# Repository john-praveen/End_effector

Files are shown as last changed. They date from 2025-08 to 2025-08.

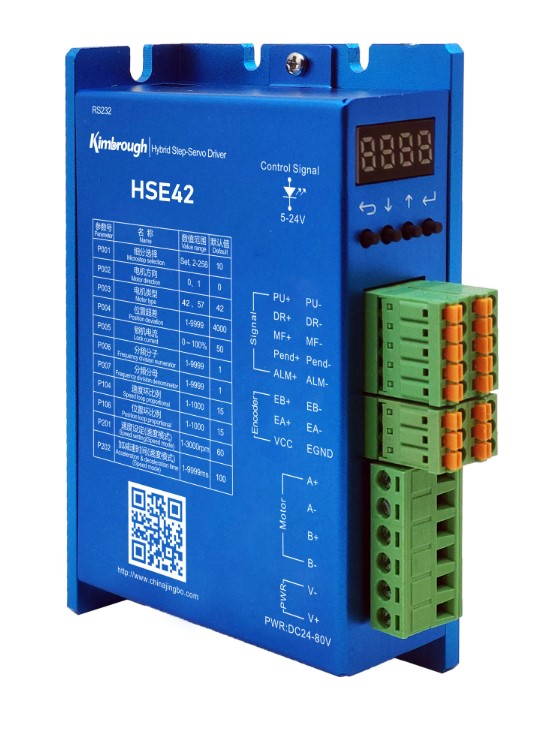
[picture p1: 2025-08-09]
Pictures/Components/Motor driver.jpg

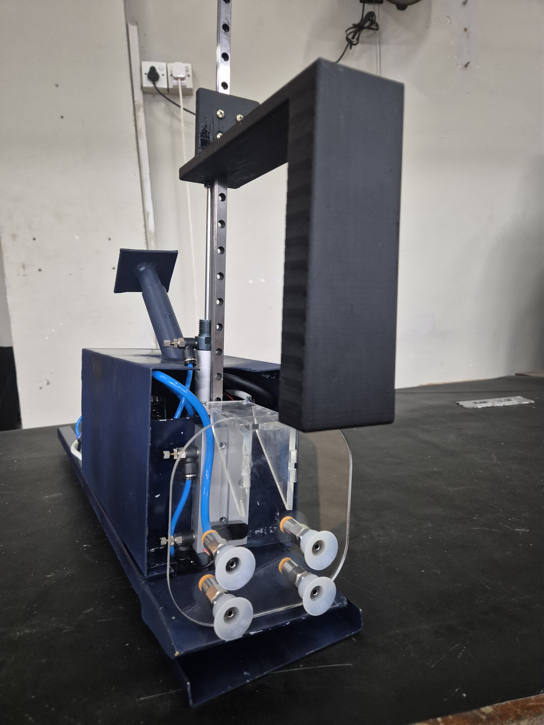
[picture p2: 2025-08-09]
Pictures/Process/3 final assembly.jpg

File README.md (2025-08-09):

# End Effector for Robotic Arm

This project is part of the **Engineering Design Realization** course at the **University of Moratuwa**. The goal is to design and implement a functional end effector that can be integrated with a robotic arm for object manipulation tasks.
The project was carried out in reference to the MCS-1-RP EOAT by WSR (https://mixedpalletizing.com/en/solutions/grippers-and-more/) and the design was a scaled down version of it.

## 🛠️ Project Overview

The end effector is designed to:
- Vaccuum grip and place boxes in warehouse/ super market settings
- Be controlled via microcontroller or external driver
- Interface with a robotic manipulator system/ Host

The project includes:
- Mechanical design (CAD)
- Electrical control (e.g., Pneumatic controls,motor drivers, communication with the host)
- Firmware (AVR - ATMEGA 2560)
- Prototyping and testing

## 📁 Repository Structure

```
End_Effector/
├── CAD/              # 3D models and design files
├── Firmware/         # Microcontroller code (AVR)
├── Schematics_PCB/   # Circuit diagrams
├── Images/           # Build photos or diagrams
└── README.md         # Project documentation
```

## 🔧 Tools & Technologies

- CAD Software:SolidWorks
- Microcontroller: ATMEGA 2560
- Actuators: Stepper motor with encoder feedback/ Single and double rod pneumatic pistons/ Vaccuum suction cups
- Programming Language: C/C++

##This project is a joint effort of
- Muftee Mysaan
- Kavishka Jayakody
- Pravindu Gunathilaka
- Rajinthan Rajeshkumar
- John Praveen
- Nilakna Warusavithana
- Venumi Gunasekara

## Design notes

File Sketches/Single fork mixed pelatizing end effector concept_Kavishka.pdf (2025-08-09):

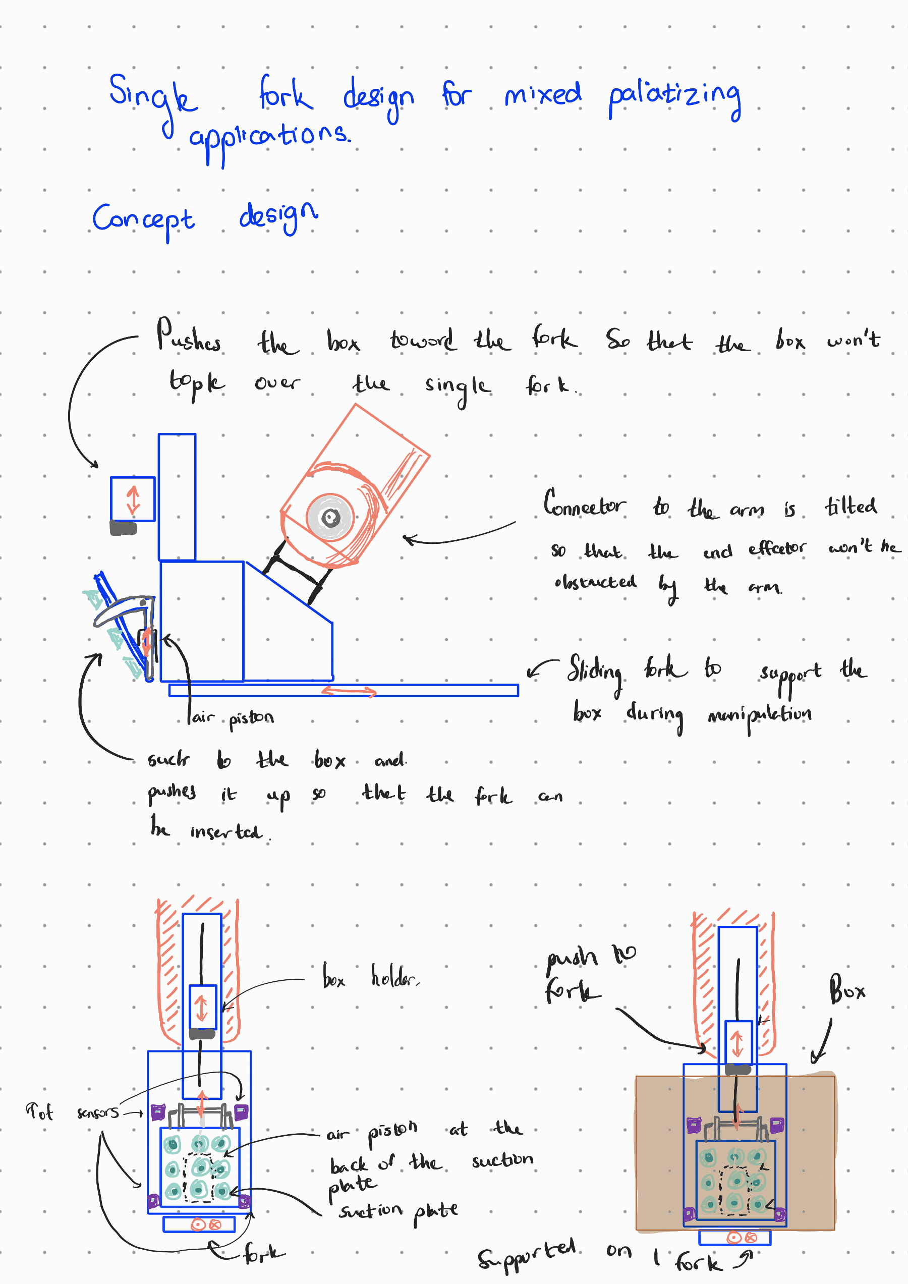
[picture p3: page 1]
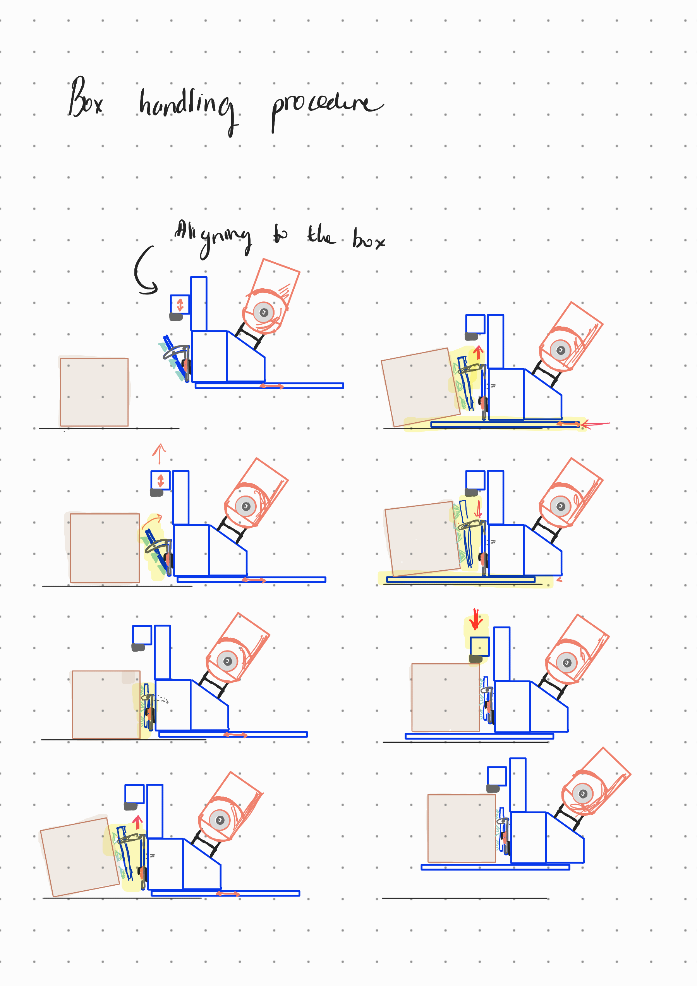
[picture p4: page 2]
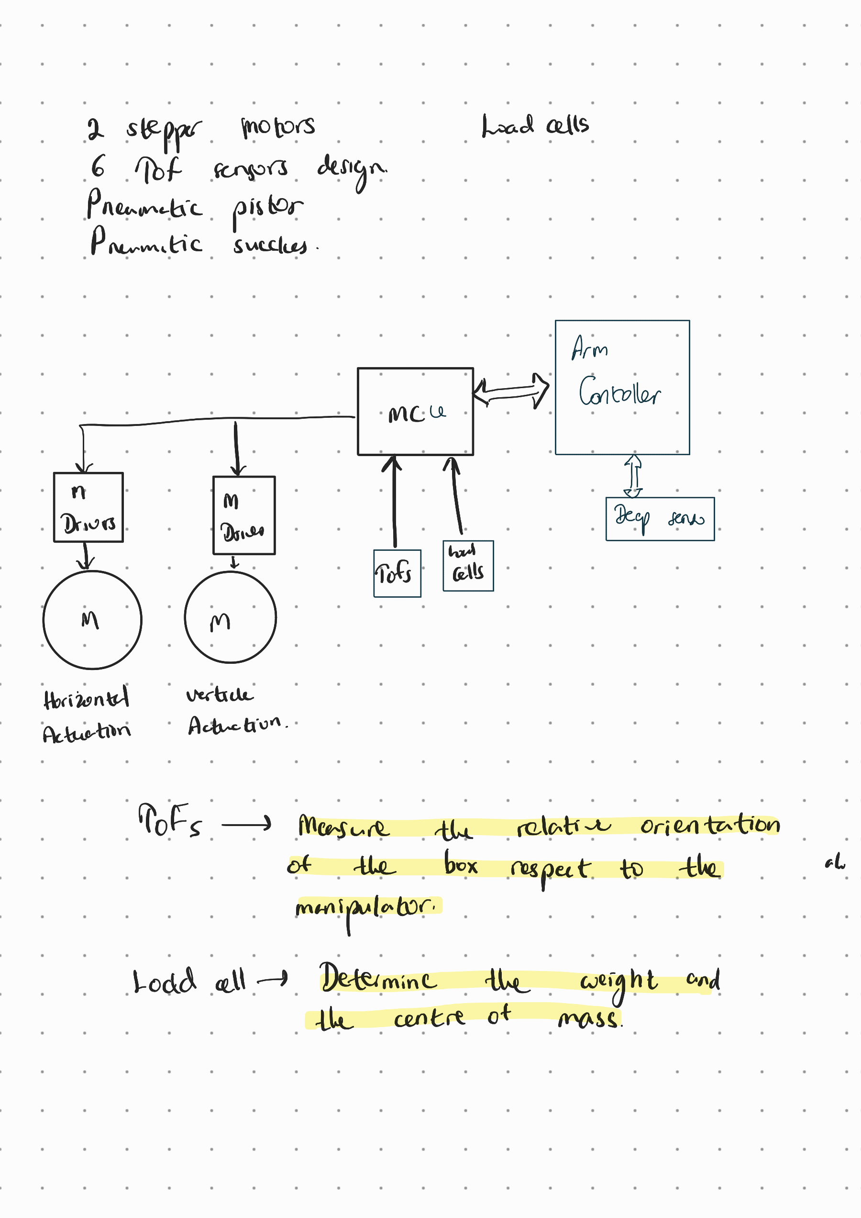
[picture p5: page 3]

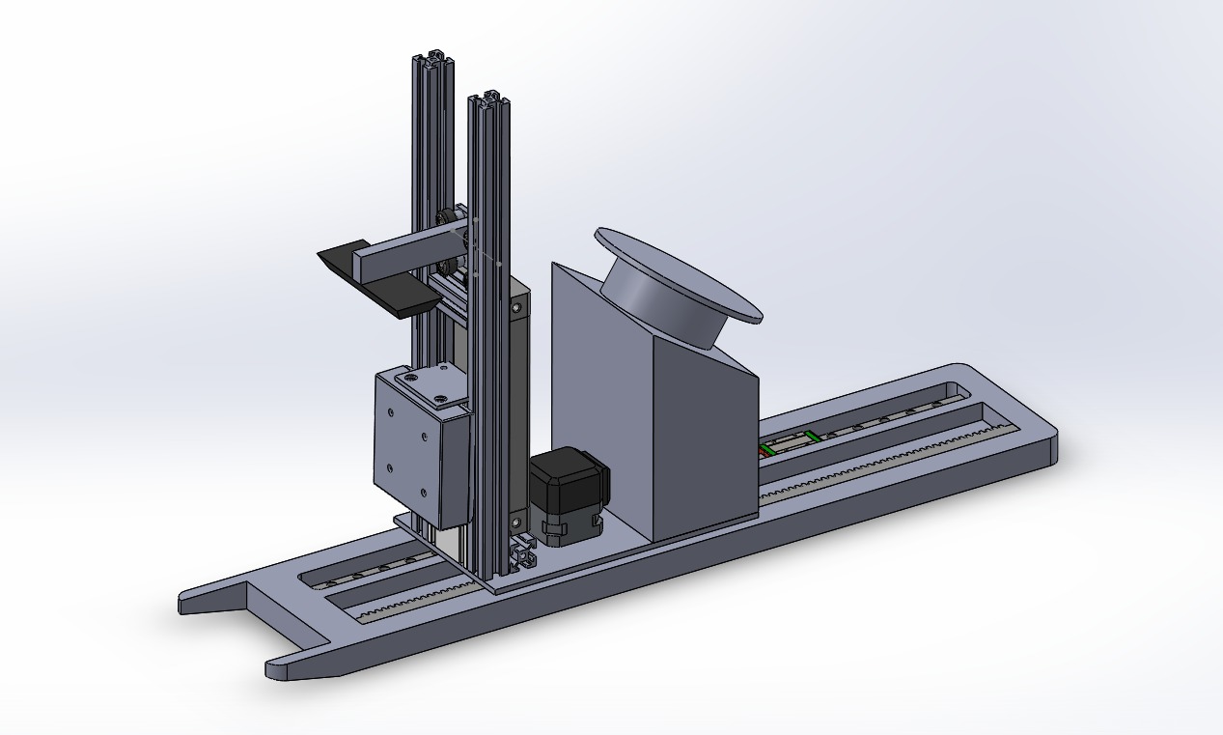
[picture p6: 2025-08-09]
Pictures/Concepts/3D Concept 1.jpg

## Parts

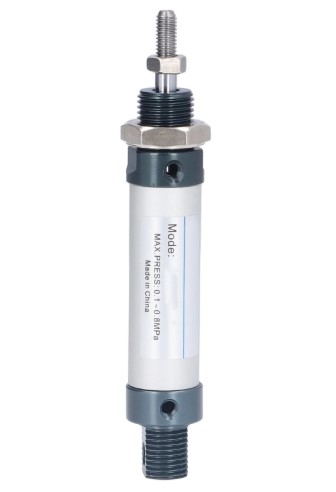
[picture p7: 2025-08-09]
Pictures/Components/single rod cylinder.jpg

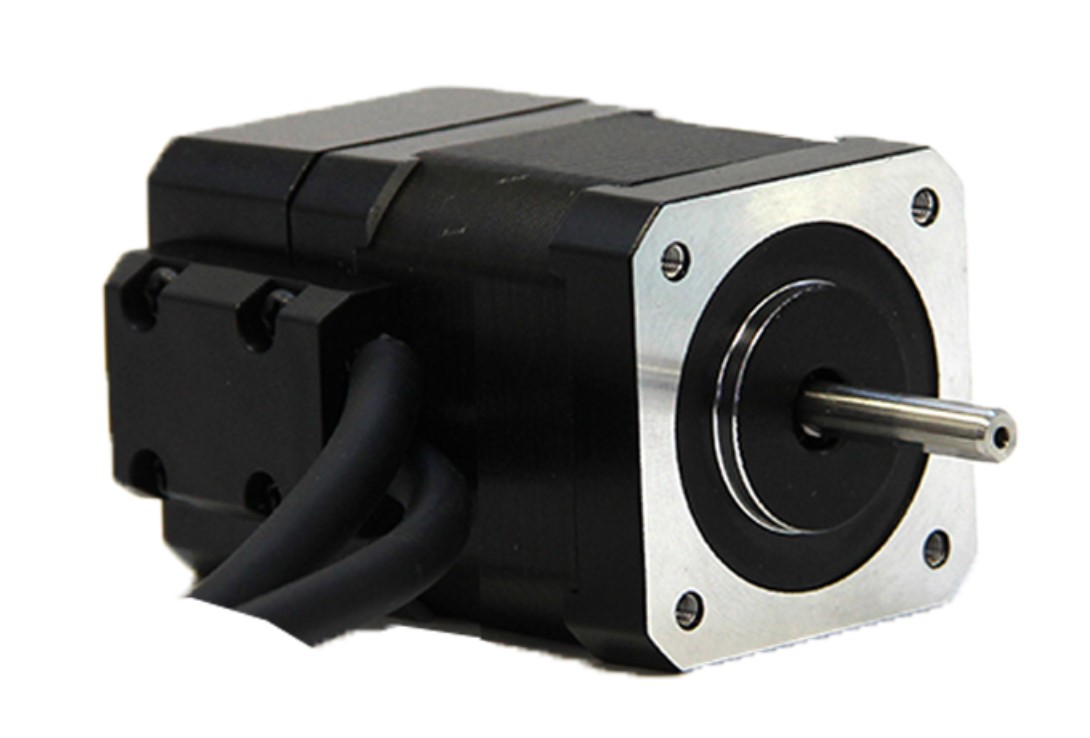
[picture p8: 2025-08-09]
Pictures/Components/Stepper motor.jpg

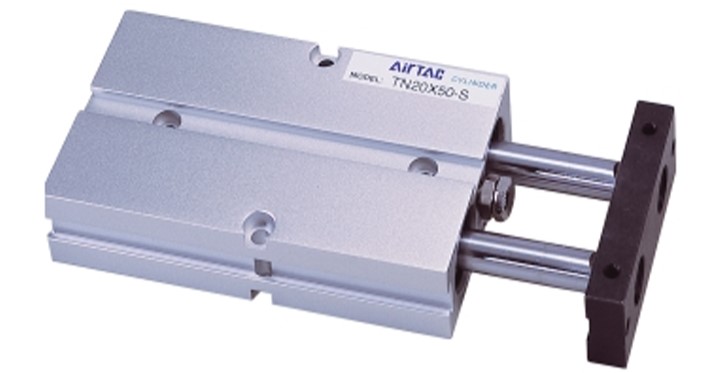
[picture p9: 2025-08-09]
Pictures/Components/double rod cylinder.jpg

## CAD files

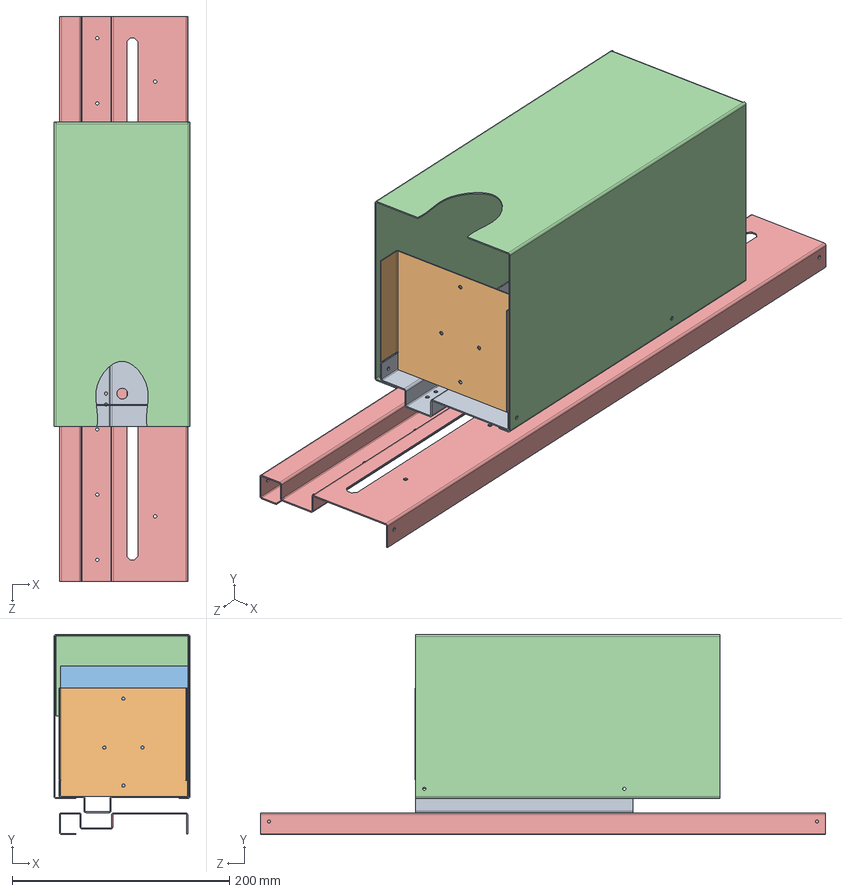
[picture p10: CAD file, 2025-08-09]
3D Models/Sheet metal/Assembly.SLDASM
125.0 x 184.0 x 520.0 mm
base_flange
front_plate
Backplate
Outer Cover
fork

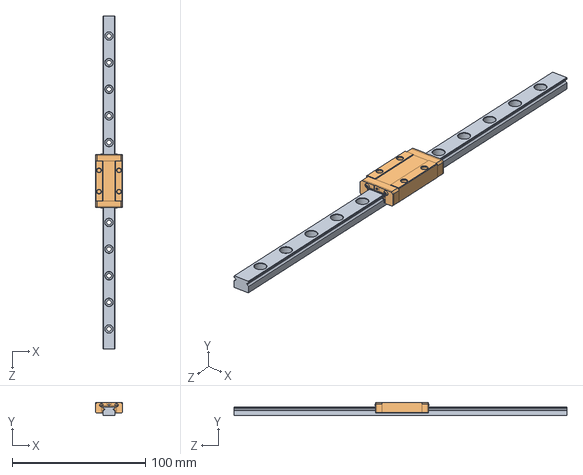
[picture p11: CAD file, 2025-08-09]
3D Models/guide rails/ver.2/MGN9-250.SLDASM
20.0 x 10.0 x 250.0 mm
MGN9
MGN9-H

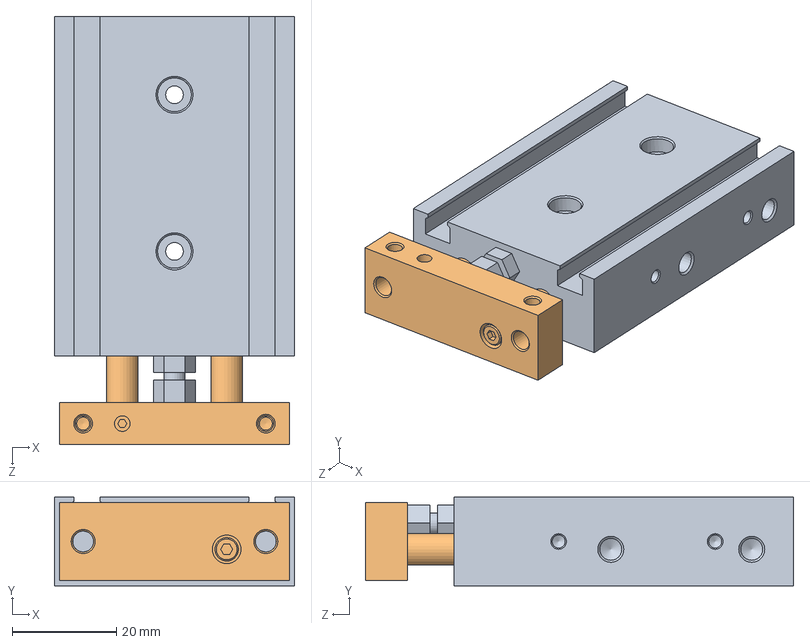
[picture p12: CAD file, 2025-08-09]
3D Models/Pneumatics/CXSM10-10/CXSM10-10.SLDASM
46.0 x 17.0 x 82.0 mm
CXSM10-10_cyl_cxs
CXSM10-10_pr_cxs

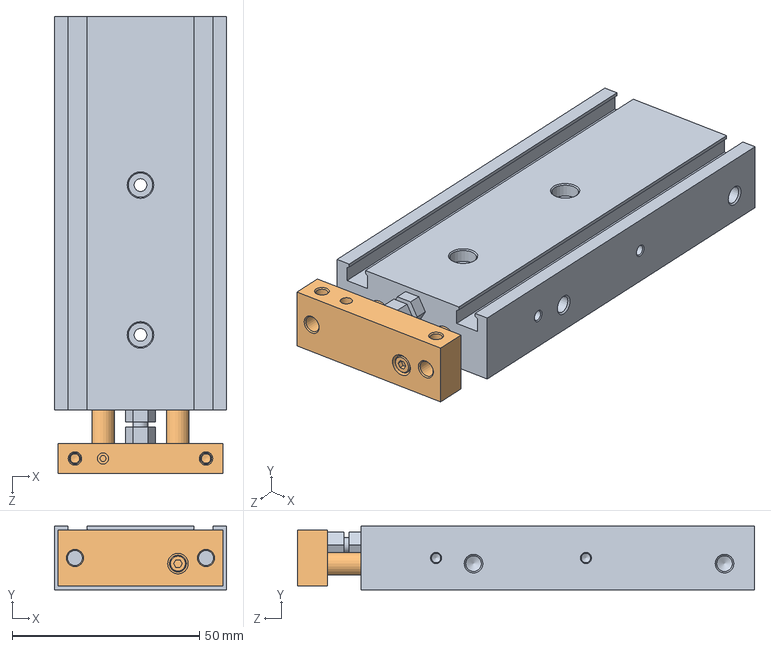
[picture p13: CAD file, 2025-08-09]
3D Models/Pneumatics/CXSM10-50/CXSM10-50.SLDASM
46.0 x 17.0 x 122.0 mm
CXSM10-50_cyl_cxs
CXSM10-50_pr_cxs

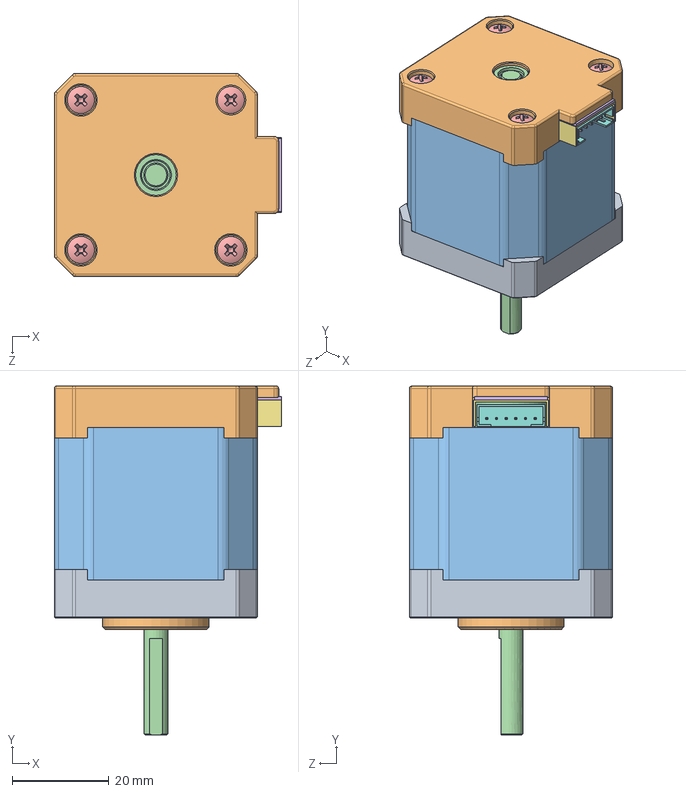
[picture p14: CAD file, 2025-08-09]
3D Models/Stepper motor/NEMA 17 Stepper Motor 48mm/NEMA 17 Stepper Motor 48mm.SLDASM
47.0 x 72.2 x 42.0 mm
Cuerpo007 x 6
Cuerpo
Cuerpo002
Cuerpo003
M3x37-Tornillo x 4
Cuerpo004
Cuerpo005
Cuerpo006
Cuerpo008
Cuerpo001

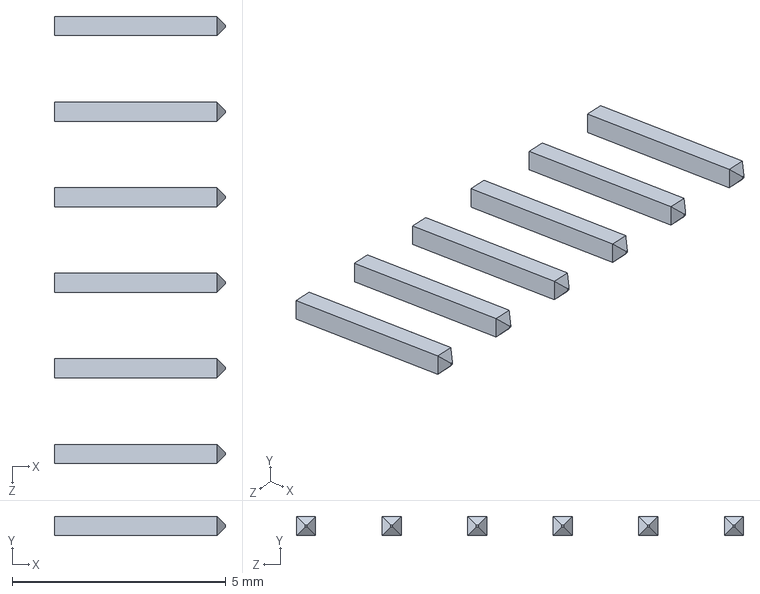
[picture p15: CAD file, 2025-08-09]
3D Models/Stepper motor/NEMA 17 Stepper Motor 48mm/Pines.SLDASM
4.00 x 0.45 x 10.4 mm
Cuerpo007 x 6

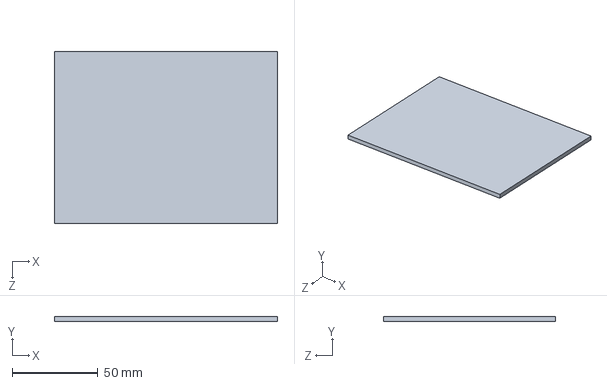
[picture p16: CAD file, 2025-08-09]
3D Models/base/Base.SLDPRT
130.0 x 3.00 x 100.0 mm

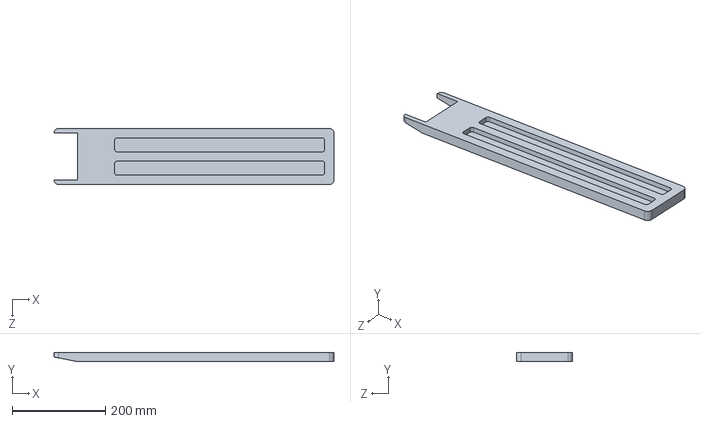
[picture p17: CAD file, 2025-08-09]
3D Models/fork/fork.SLDPRT
600.0 x 20.0 x 120.0 mm

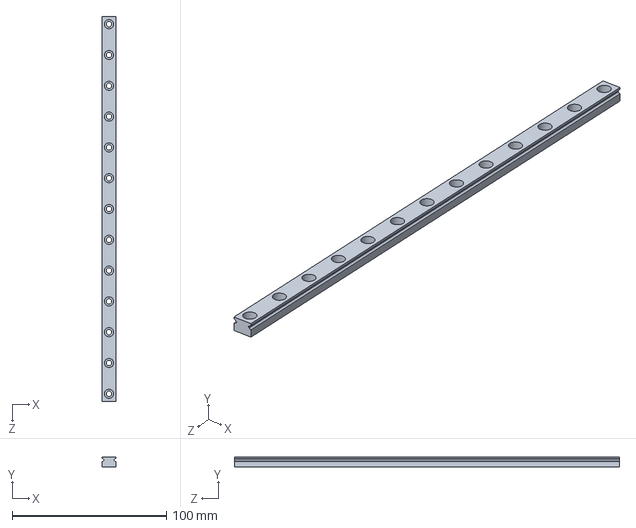
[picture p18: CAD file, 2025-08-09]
3D Models/guide rails/v1_MGN9_250.SLDPRT
9.00 x 6.50 x 250.0 mm

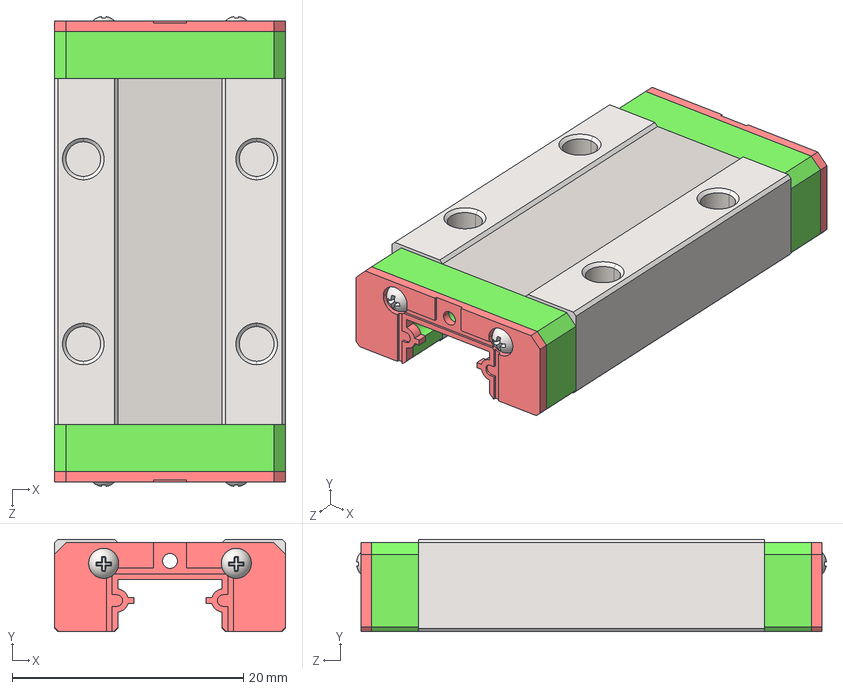
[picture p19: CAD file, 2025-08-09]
3D Models/guide rails/ver.2/MGN9-H.STEP
20.0 x 8.00 x 40.7 mm

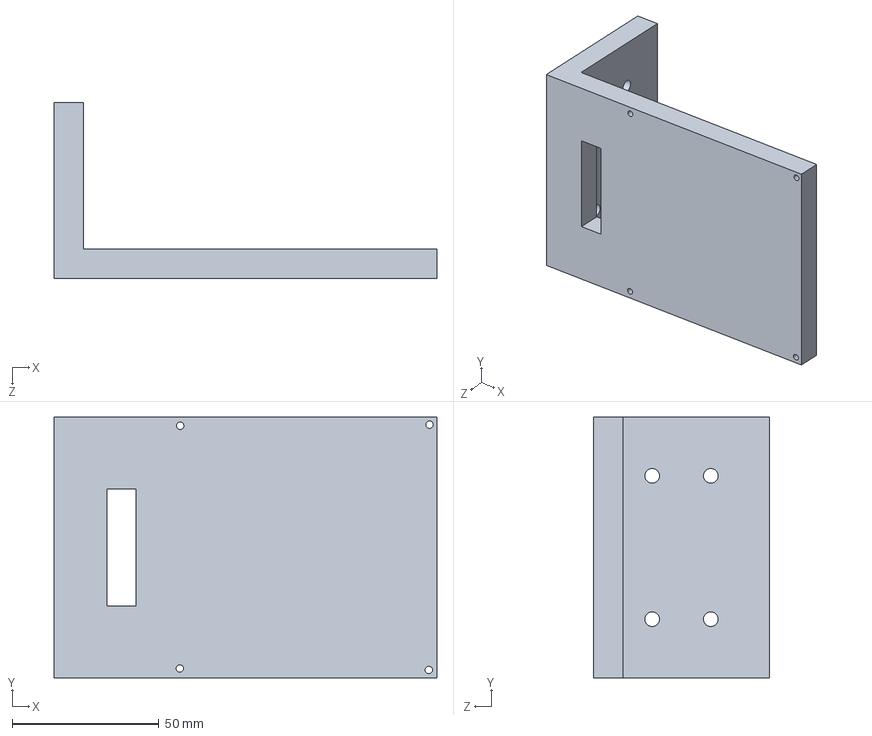
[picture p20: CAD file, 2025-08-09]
3D Models/John/end_effector_solidworks/parts/pcb_mount_F.SLDPRT
130.7 x 88.9 x 60.0 mm

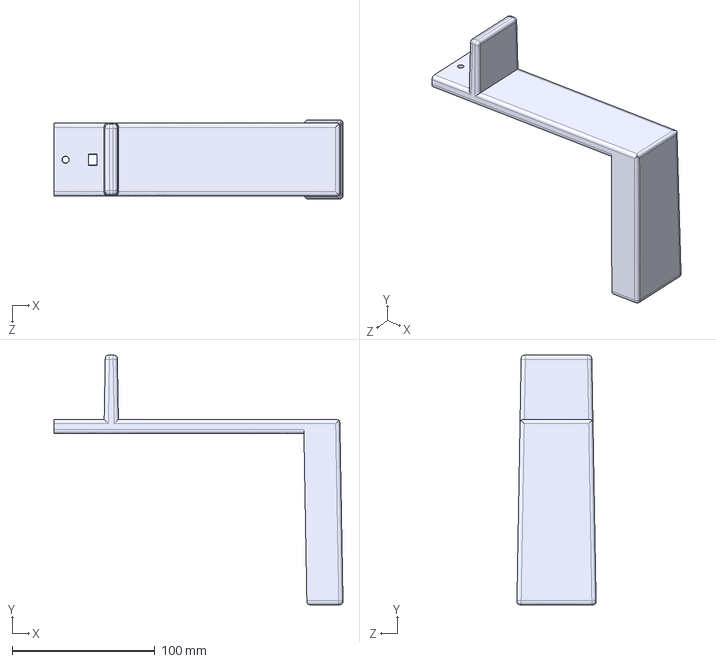
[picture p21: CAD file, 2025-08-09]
3D Models/John/end_effector_solidworks/stp/top support.STEP
202.6 x 175.0 x 55.5 mm

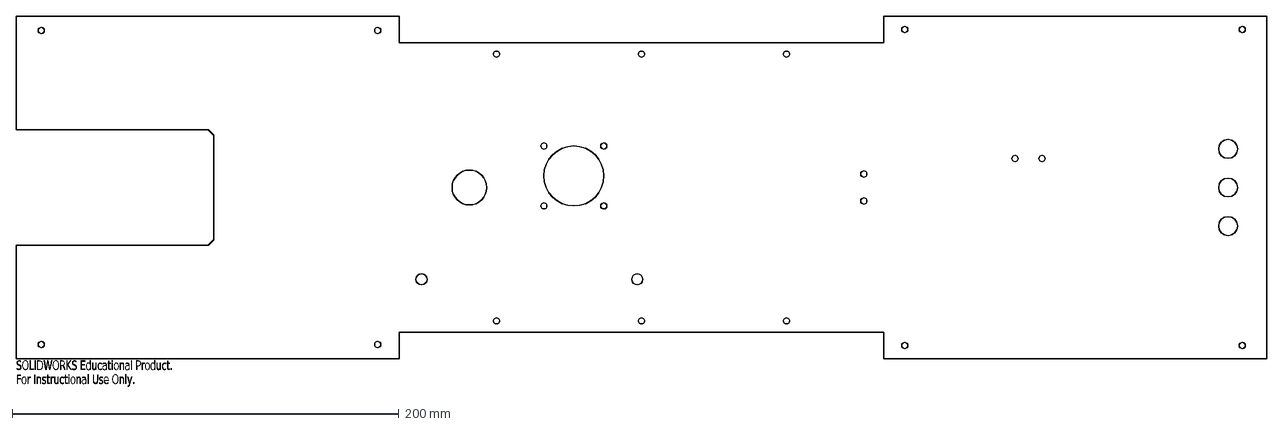
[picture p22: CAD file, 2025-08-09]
3D Models/Sheet metal/Fabrication Outputs/Flat pattern - body_flat.DXF
SOLIDWORKS Educational Product.
For Instructional Use Only.

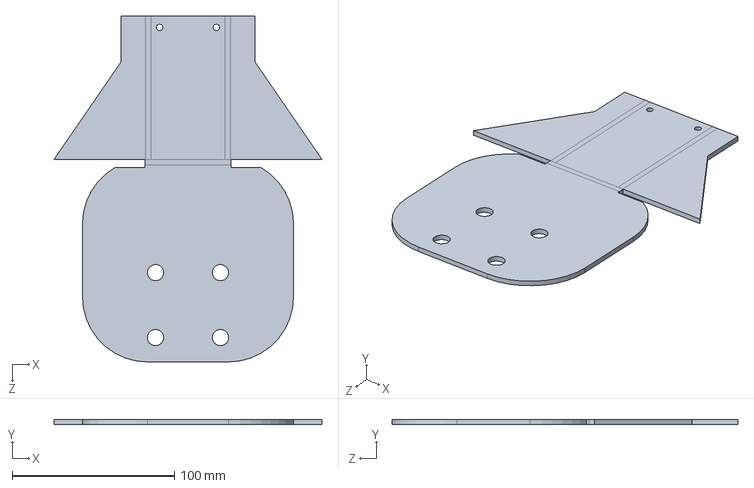
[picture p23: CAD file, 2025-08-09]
3D Models/Sheet metal/Suction Pad/sheet metal suction pad.SLDPRT
165.1 x 3.00 x 213.0 mm

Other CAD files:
3D Models/guide rails/MGN9.SLDASM
3D Models/Pneumatics/CXSM10-10/CXSM10-10_pr_cxs.sldprt
3D Models/Pneumatics/CXSM10-50/CXSM10-50_pr_cxs.sldprt
3D Models/Sheet metal/Top Support/sheet metal top support venumi.SLDPRT
3D Models/John/end_effector_solidworks/parts/top support.SLDPRT
3D Models/John/end_effector_solidworks/parts/vaccum_plate.SLDPRT
3D Models/John/end_effector_solidworks/stp/pcb_mount.STEP
3D Models/John/end_effector_solidworks/stp/vaccum_plate.STEP
3D Models/Pneumatics/CXSM10-10/CXSM10-10_cyl_cxs.sldprt
3D Models/Pneumatics/CXSM10-50/CXSM10-50_cyl_cxs.sldprt
3D Models/Sheet metal/Backplate.SLDPRT
3D Models/Sheet metal/Fabrication Outputs/Flat pattern - cover_flat.DXF
3D Models/Sheet metal/Fabrication Outputs/Flat pattern - fork_flat.DXF
3D Models/Sheet metal/Fabrication Outputs/Flat pattern - metal_back.DXF
3D Models/Sheet metal/Outer Cover.SLDPRT
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

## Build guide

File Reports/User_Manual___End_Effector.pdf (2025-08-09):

# User Manual

# End Effector

Group 07
Document Version 1.0

May 2025

## Contents

1 Preface | 3
2 Getting Started | 3
3 Control Commands | 7
4 Assembly Instructions | 8
5 Maintenance Guidelines | 12
6 Technical Specifications | 13

## 1 Preface

### 1.1 Target Audience

This document is intended for integrators who design and install complete robot applications. Personnel working with the end-effector are expected to have the following expertise:

- Basic knowledge of mechanical systems
- Basic knowledge of electronic and electrical systems
- Basic knowledge of the robot system

### 1.2 Intended Use

The end-effector is designed for grabbing objects, installed on the end effector of a robot, typically used in pick and place applications.

### 1.3 Safety Notice

A risk assessment is required for each application the end-effector is a part of. It is important that all safety instructions are followed. The safety instructions are limited to the end-effector only, and do not cover the safety precautions of a complete application.

Below are some (but not all) potentially dangerous situations.

- Entrapment of fingers between the sliding rail and the body.
- Entrapment of fingers between the rail and/or vertical stabilizer and the body.
- Objects falling out of the end-effector e.g. due to misalignment of robot arm or high acceleration from robot arm.

## 2 Getting Started

### 2.1 Mounting

The end-effector is attached to the robot arm using a welding neck flange, following the ISO 9409-1 standardized mounting interface. Proper alignment is ensured through the use of suitable screws positioned on a pitch circle diameter.

Mounting Parameters (ISO 9409-1)

- d1 : 37.5 | (Pitch Circle Diameter)
- N : 4 | (Number of threaded holes)
- d4 : M6 | (Thread size of holes)

### 2.2 Operation

### 2.2.1 Communication with PC

The end-effector communicates the following information with the robot controller PC:

- Angle: Angle between the end-effector and the object to be picked.
- Distance: Distance between the end-effector and the object to be picked.

The robot controller is expected to ensure proper alignment and positioning of the end-effector for successful gripping operation.

### 2.2.2 Picking the Object

Once proper alignment and positioning is ensured, the pick command must be issued to the end-effector by the robot controller PC.

Once the command is given, the following steps will take place:

- Suction: The vacuums will activate and suction will hold the object against the suction pad.
- Raising: The suction pad will rise up, lifting the side of the object.
- Rail: The rail will slide under the object.
- Top Support: The vertical stabilizer will move down onto the object, providing further stabilization.
- Remove Suction: Suction will be removed once the object is stable.

### 2.2.3 Transporting the Object

The robot arm is responsible for transporting the object to the correct destination and ensuring correct alignment.

### 2.2.4 Placing the Object

Once proper alignment and positioning is ensured, the place command must be issued to the end-effector by the robot controller PC.

Once the command is given, the following steps will take place:

- Rail: The sliding rail will move out from under the object, resting the object at the target location.
- Top Support: The top support will raise and the object will be completely released by the end-effector.

### 2.3 Mechanical Dimensions

### 2.3.1 Fork

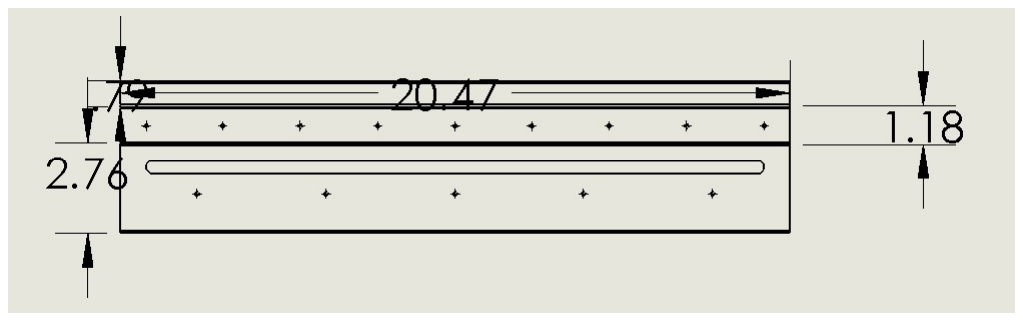
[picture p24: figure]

Figure 1: Fork Dimensions

### 2.3.2 Base Flange

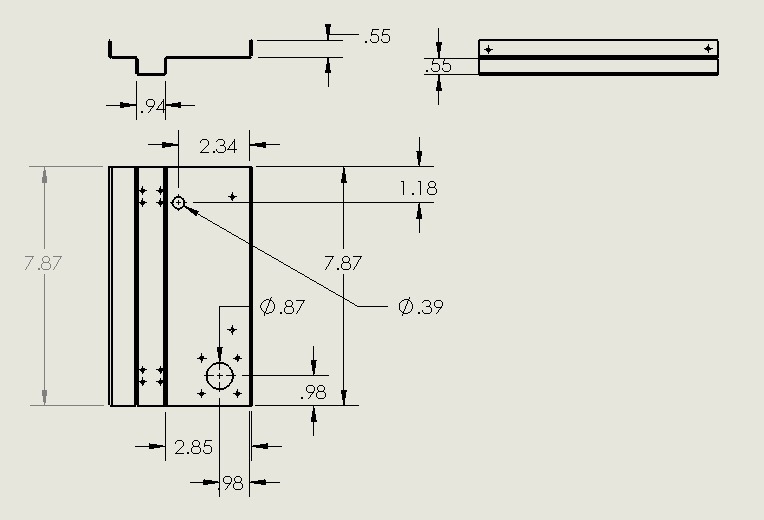
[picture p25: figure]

Figure 2: Base Flange Dimensions

### 2.3.3 Outer Cover

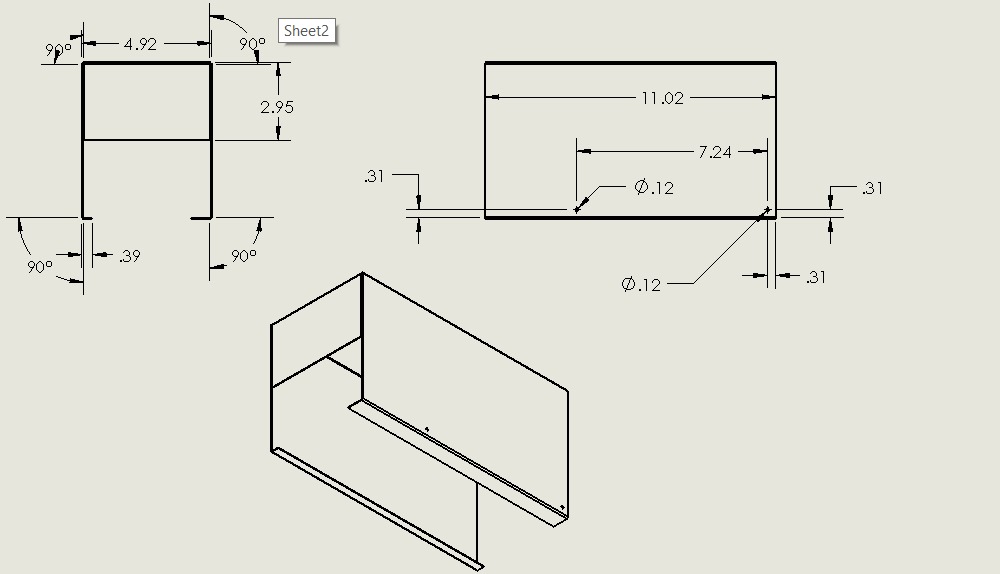
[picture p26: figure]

Figure 3: Outer Cover Dimensions

### 2.3.4 Back Plate

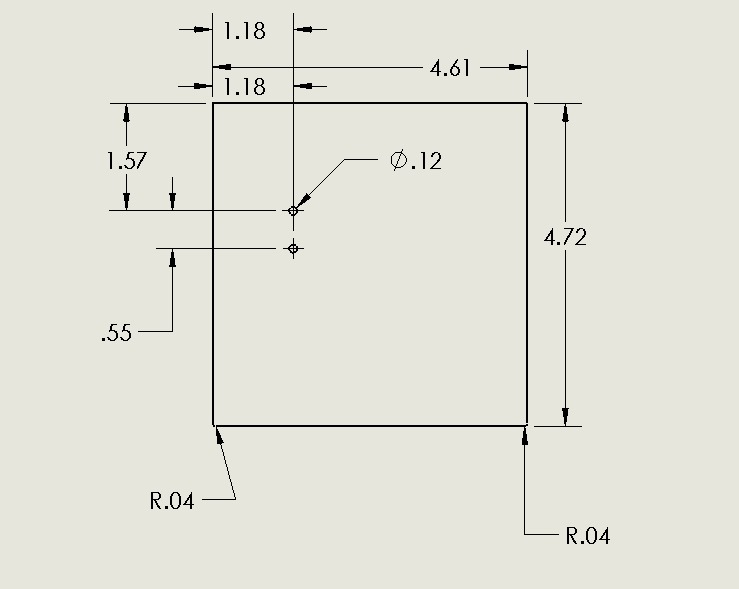
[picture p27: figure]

Figure 4: Back Plate Dimensions

### 2.3.5 Front Plate

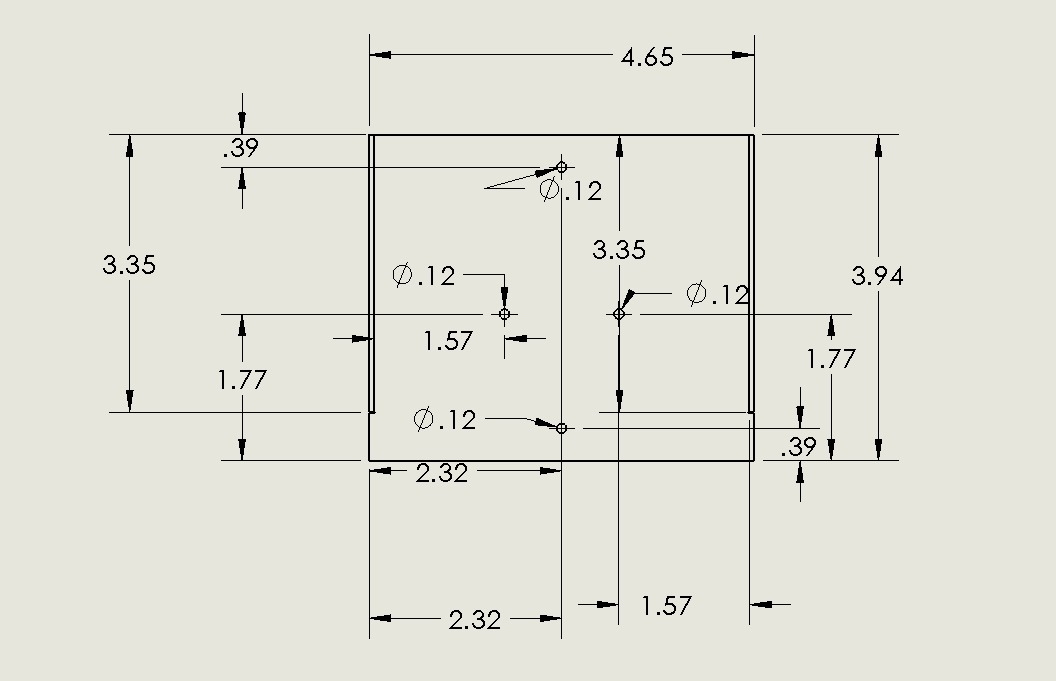
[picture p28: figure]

Figure 5: Front Plate Dimensions

### 2.3.6 Gear wheel and Rack

- Pinion Gear:

– Module: 1 mm

– Teeth: 20

– Pitch Diameter: 20 mm

– Bore: 5mm (D-type with cut at 4.5mm)

- Rack:

– Module: 1 mm

– Face width: ≥ 10 mm

– Length: 500 mm

### 2.4 Load Capacity

The end-effector has an operational capacity of 1kg uniformly weighted boxes. Exceeding the weight limit may result in structural failure and/or injury.

### 2.5 Connections

### 2.5.1 Pneumatic Connections

Guide the connections for the solenoids and the vacuum suction pads through the groove cut into the base.

Connect 4mm PU tubes from the two double solenoids to the single rod and double rod pistons (each piston must have two tubes.) Connect 4mm tubes from the single solenoid to the suction cups.

Connect the vacuum to the single solenoid and compressor the the two double solenoids using 6mm PU tubes. The solenoid tubes and vacuum tubes must be connected to a compressor with the following specifications.

### 2.5.2 Power Supply

The gripper is designed to operate with a 24V DC power supply. Ensure the power source is regulated and within the specified voltage range for safe and reliable operation. Guide the power supply through the same groove in the base.

Table 1: Pneumatic Specifications

Parameter | Value
Pressure | 6 bar
Air Supply Tube Diameter | Ø12 mm
Airflow (including vacuum) | 40 l/min
Minimum Air Quality | ISO 8573-1:2010 7 : 4 : 4

## 3 Control Commands

The end-effector is controlled via UART communication with the host system (typically a PC or microcontroller). The following commands must be transmitted over UART to initiate the respective operational sequences. The communication protocol uses 8 data bits, no parity, and 1 stop bit (8N1), as shown in Figure 6.

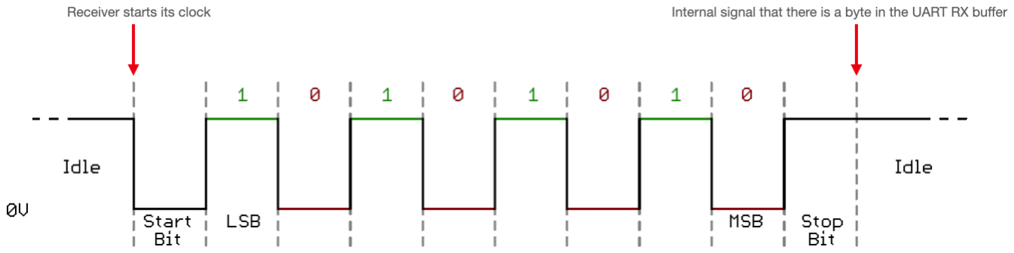
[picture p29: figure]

Figure 6: UART Protocol: 8 data bits, 1 stop bit

### 3.1 Pick Command

To initiate the picking sequence, transmit the command CMD GRIPPER PICK. This command autonomously executes the full gripping and lifting process. No further step-by-step commands are required.

### 3.2 Place Command

To initiate the release sequence, transmit the command CMD GRIPPER RELEASE. This will fully execute the object release process, including the lowering and unclamping actions.

### 3.3 Debug Commands

For system-level debugging and verification, the following individual control commands can be used. These allow manual actuation of subsystems for testing. Warning: Ensure the workspace around the end-effector is clear before issuing debug commands to avoid damage or injury.

- CMD TOP GRIPPER
- CMD FORK
- CMD VACUUM GRIPPER
- CMD VACUUM UP

## 4 Assembly Instructions

Follow the steps outlined below to correctly assemble the end-effector. All fasteners specified are M3 unless otherwise stated.

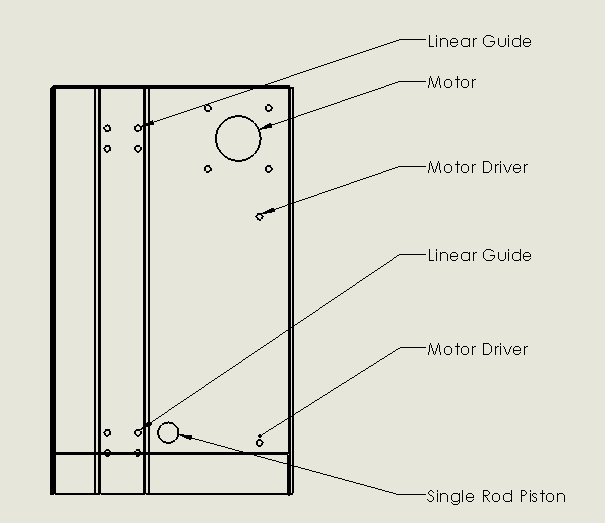
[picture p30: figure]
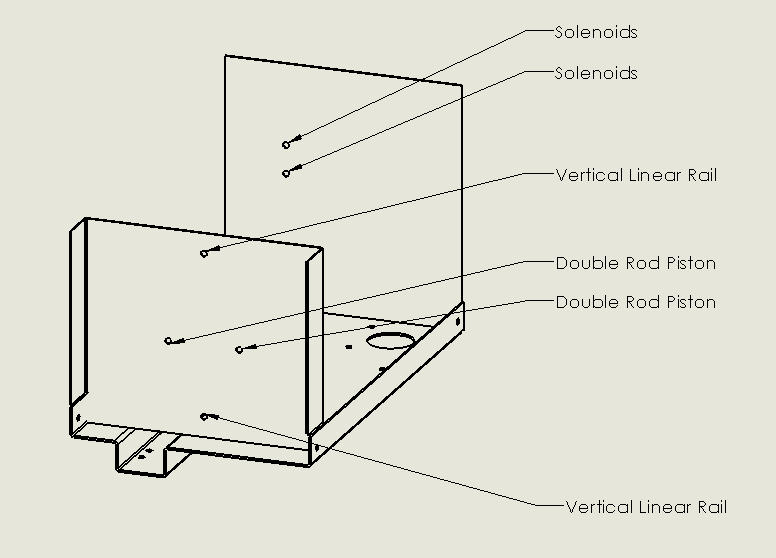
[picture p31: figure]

Figure 7: Top View - Base | Figure 8: Dimetric View - Base

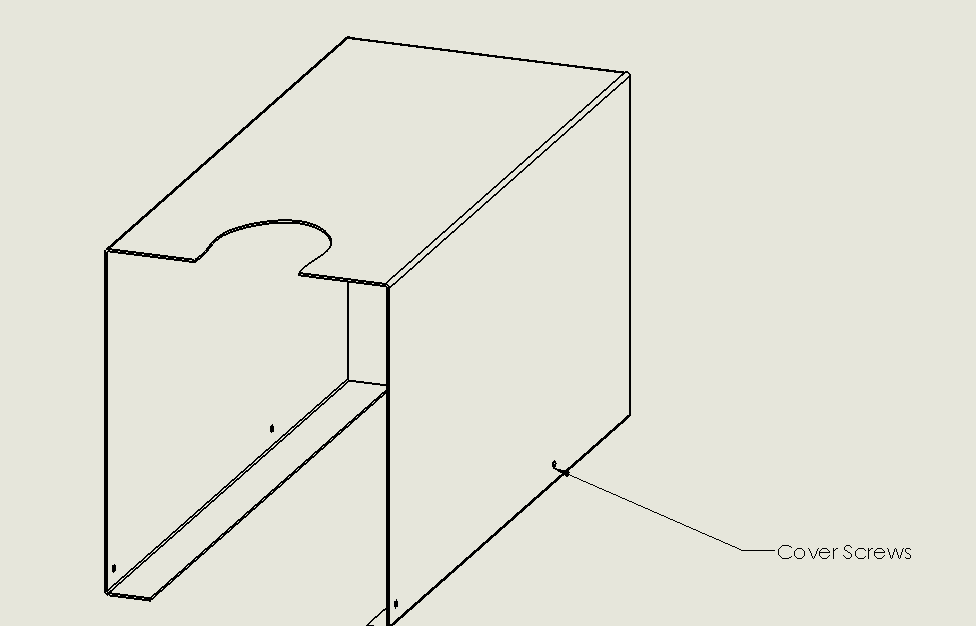
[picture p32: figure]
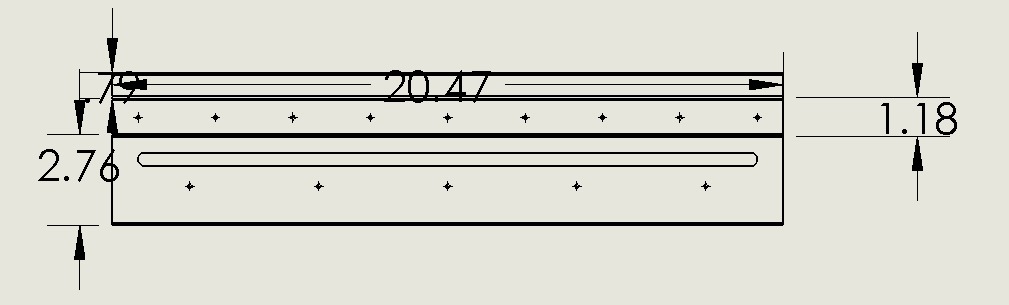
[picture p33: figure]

Figure 9: Cover | Figure 10: Fork

### 4.1 Motor Mounting

Secure the motor to the base using four 1/4-inch M3 screws and M3 nuts. Ensure that the motor shaft extends downward through the designated central opening in the base.

### 4.2 Installation of Linear Guides and Rail

Attach the linear guides to the underside of the base using four 1/4-inch M3 screws inserted from the top side. The alignment slot of the linear guide must correspond precisely with the groove on the base. After installation, insert the linear rail into the linear guide track.

### 4.3 Fork Assembly

Position the assembled base and linear rail onto the fork component, aligning the end holes of the rail with the predrilled mounting holes on the fork groove. Secure the linear rail to the fork using three 1/4-inch M3 screws and M3 nuts. Mount the rack to the underside of the fork using three M3 screws and nuts, inserted from the top side. Install the gear wheel onto the motor shaft, ensuring proper engagement with the rack teeth to allow smooth linear motion. Once complete, insert the lower fork section into the upper fork structure. Align the screw holes and fasten them using four 1/4-inch M3 screws.

### 4.4 Vertical Rail and Top Support

Fix the vertical linear rail to the base using two M3 screws and nuts, fastened from the inside. Couple the linear guide to the top support bracket, and slide the vertical rail into the guide channel to complete the vertical axis assembly.

### 4.5 Solenoids and Piston Installation

Mount the double and single solenoids to the rear panel of the base using two 4-inch M3 screws and M3 nuts. Secure the double-rod pneumatic cylinder to the front of the base using two 1/2-inch M3 screws and nuts. Attach the single-rod pneumatic piston to the base using a 12 mm bolt from underneath. Fix the top support to the piston shaft to complete the actuator assembly.

### 4.6 Motor Driver

Fasten the motor driver horizontally to the base using two 1/4-inch M3 screws and M3 nuts. Ensure that the back plate faces outward and the terminal connectors face upward.

### 4.7 PCB Integration

Install the PCB standoffs to the base and mount the PCB using eight 1/4-inch M3 screws and M3 nuts.

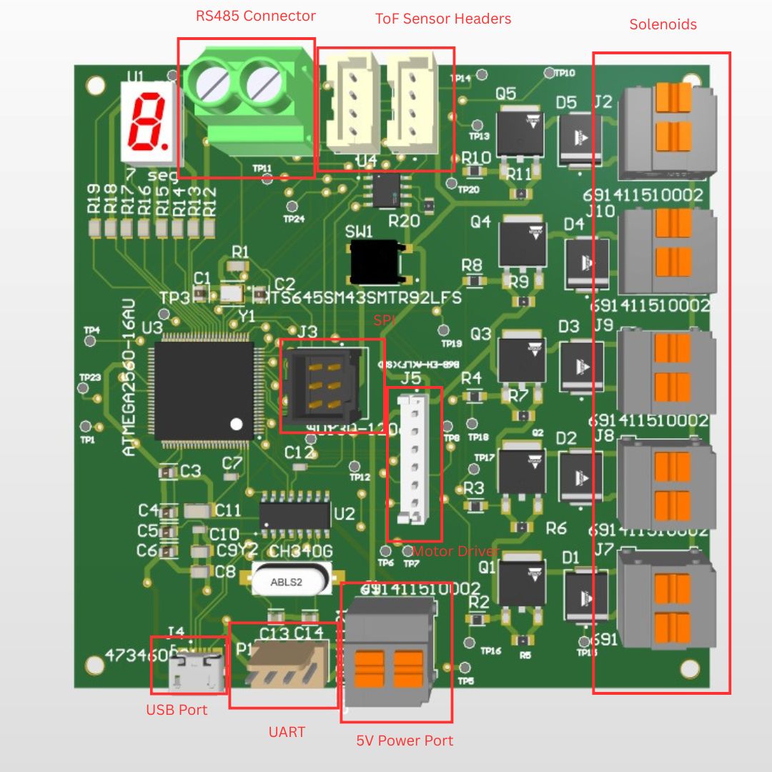
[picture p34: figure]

Figure 11: Main Connectors Annotation

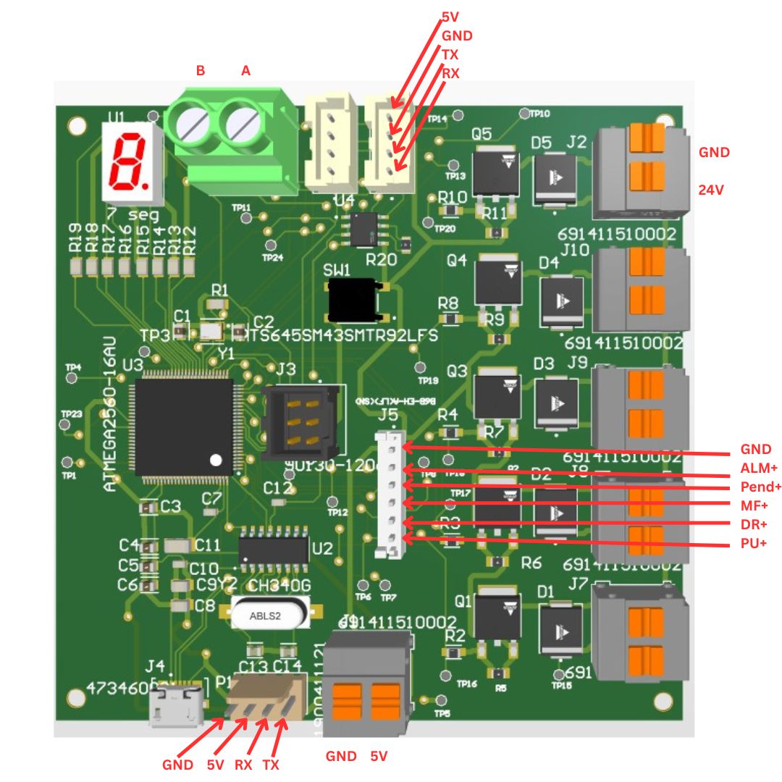
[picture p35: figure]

Figure 12: Pin Mapping

Refer to the annotated 3D PCB view for identifying the correct headers. Carefully install the ToF sensor and motor driver module onto the designated connectors as labeled. Ensure that each module is connected to its respective header—UART, SPI, solenoid, ToF, and motor driver—as shown in the pin mapping. Double-check the orientation and pin alignment to match the annotated pin assignments. Incorrect connections may result in malfunction or hardware damage.

### 4.8 Suction Plate Installation

Secure the suction plate to the top of the double-rod piston using two 1/4-inch M3 screws and M3 nuts. Connect the 4mm tubes to the suction cups and route them over the top and through the groove in the base.

### 4.9 Electrical and Pneumatic Routing

Neatly route all electrical wires and pneumatic tubing through the designated groove channel in the base.

### 4.10 Final Assembly and Mounting

Place the top enclosure over the base and secure it using four M3 screws and nuts. Finally, attach the fully assembled end-effector to the robot arm flange using a 6 mm screw and nut.

Once completed, the end effector should look similar to the following images:

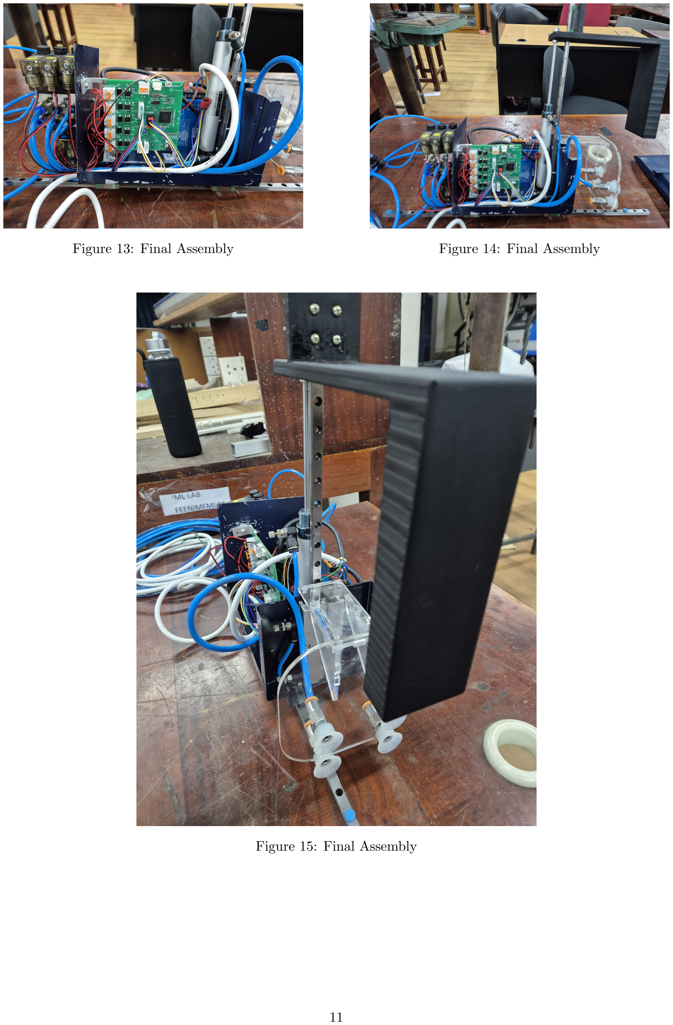
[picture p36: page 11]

Figure 13: Final Assembly | Figure 14: Final Assembly

Figure 15: Final Assembly

## 5 Maintenance Guidelines

This section outlines the preventive maintenance procedures required to ensure the long-term reliability and performance of the end-effector. All maintenance activities should be logged with date, technician name, and observations.

### 5.1 Closed-Loop Stepper Motor and Gear Mechanism

Interval: Every 250 operating hours or monthly (whichever comes first)

- Perform visual inspection for dust, debris, and oil contamination.
- Check axial and radial play in the motor shaft. Replace bearings if excessive movement is detected.
- Inspect gear teeth and rack for signs of wear, backlash, or misalignment.
- Apply high-performance synthetic gear lubricant to the gear teeth and rack.
- Conduct encoder feedback diagnostics to verify closed-loop accuracy.

### 5.2 Linear Guides and Rail

Interval: Every 100 operating hours

- Clean linear guideways with lint-free cloth and reapply lithium-based grease.
- Inspect for abnormal noise or resistance during linear motion; verify alignment and smoothness.
- Use dial indicator or laser alignment tools to detect rail deflection or misalignment.

### 5.3 Pneumatic Solenoids and Cylinders

Interval: Weekly visual inspection, full functional test every 200 cycles

- Inspect PU tubing for cracks, brittleness, or leaks.
- Verify actuation of all three double solenoids and both pistons (single and double rod) via manual override.
- Conduct air leak test using soap solution or ultrasonic leak detector.
- Check piston rods for surface pitting or sticking; re-lubricate or replace seals as necessary.
- Validate response time and holding pressure using a calibrated pneumatic test bench.

### 5.4 Vacuum Plate Assembly

Interval: Biweekly

- Check for airtight seals and vacuum pressure drop using a digital vacuum gauge.
- Inspect suction cups for deformation or wear; replace if rigidity is compromised.
- Clean contact surfaces to maintain optimal grip efficiency.

### 5.5 PCB and Electrical Components

Interval: Monthly

- Inspect PCB for discoloration, corrosion, or loose connectors.
- Check signal continuity and voltage outputs using a multimeter or oscilloscope.
- Verify motor driver thermal state under load; ensure proper heat dissipation.
- Ensure no cable insulation degradation near high-vibration areas.

### 5.6 Top Support and Vertical Linear Rail

Interval: Every 200 cycles or bi-monthly

- Inspect linear motion and guide block alignment with vertical rail.
- Ensure top support fasteners are tightened to specification.
- Check the coupling between the top support and single rod piston for wear or instability.

### 5.7 General Preventive Maintenance

- Ensure all fasteners are tightened.
- Remove dust and particulates using compressed air or vacuum cleaning.
- Update firmware and perform diagnostics using onboard tools as per controller documentation.
- Record all maintenance actions in the maintenance logbook or digital system.

Note: Always disconnect electrical and pneumatic power before performing maintenance. Use personal protective equipment (PPE) in accordance with safety protocols.

## 6 Technical Specifications

Table 2: Technical specifications of the End-Effector.

Technical Data | Min | Typical | Max | Units
Compressor Pressure | | 8 | | Bar
Vacuum Pressure | 60 | | 80 | %
Operating voltage | | 24 | | V DC
Power Rating | | | 72W | W
Maximum Current | | | 3 | A
Ambient operating temperature | 5 | | 50 | ◦C
Storage temperature | 0 | | 60 | ◦C
Product weight | | 6 | | kg

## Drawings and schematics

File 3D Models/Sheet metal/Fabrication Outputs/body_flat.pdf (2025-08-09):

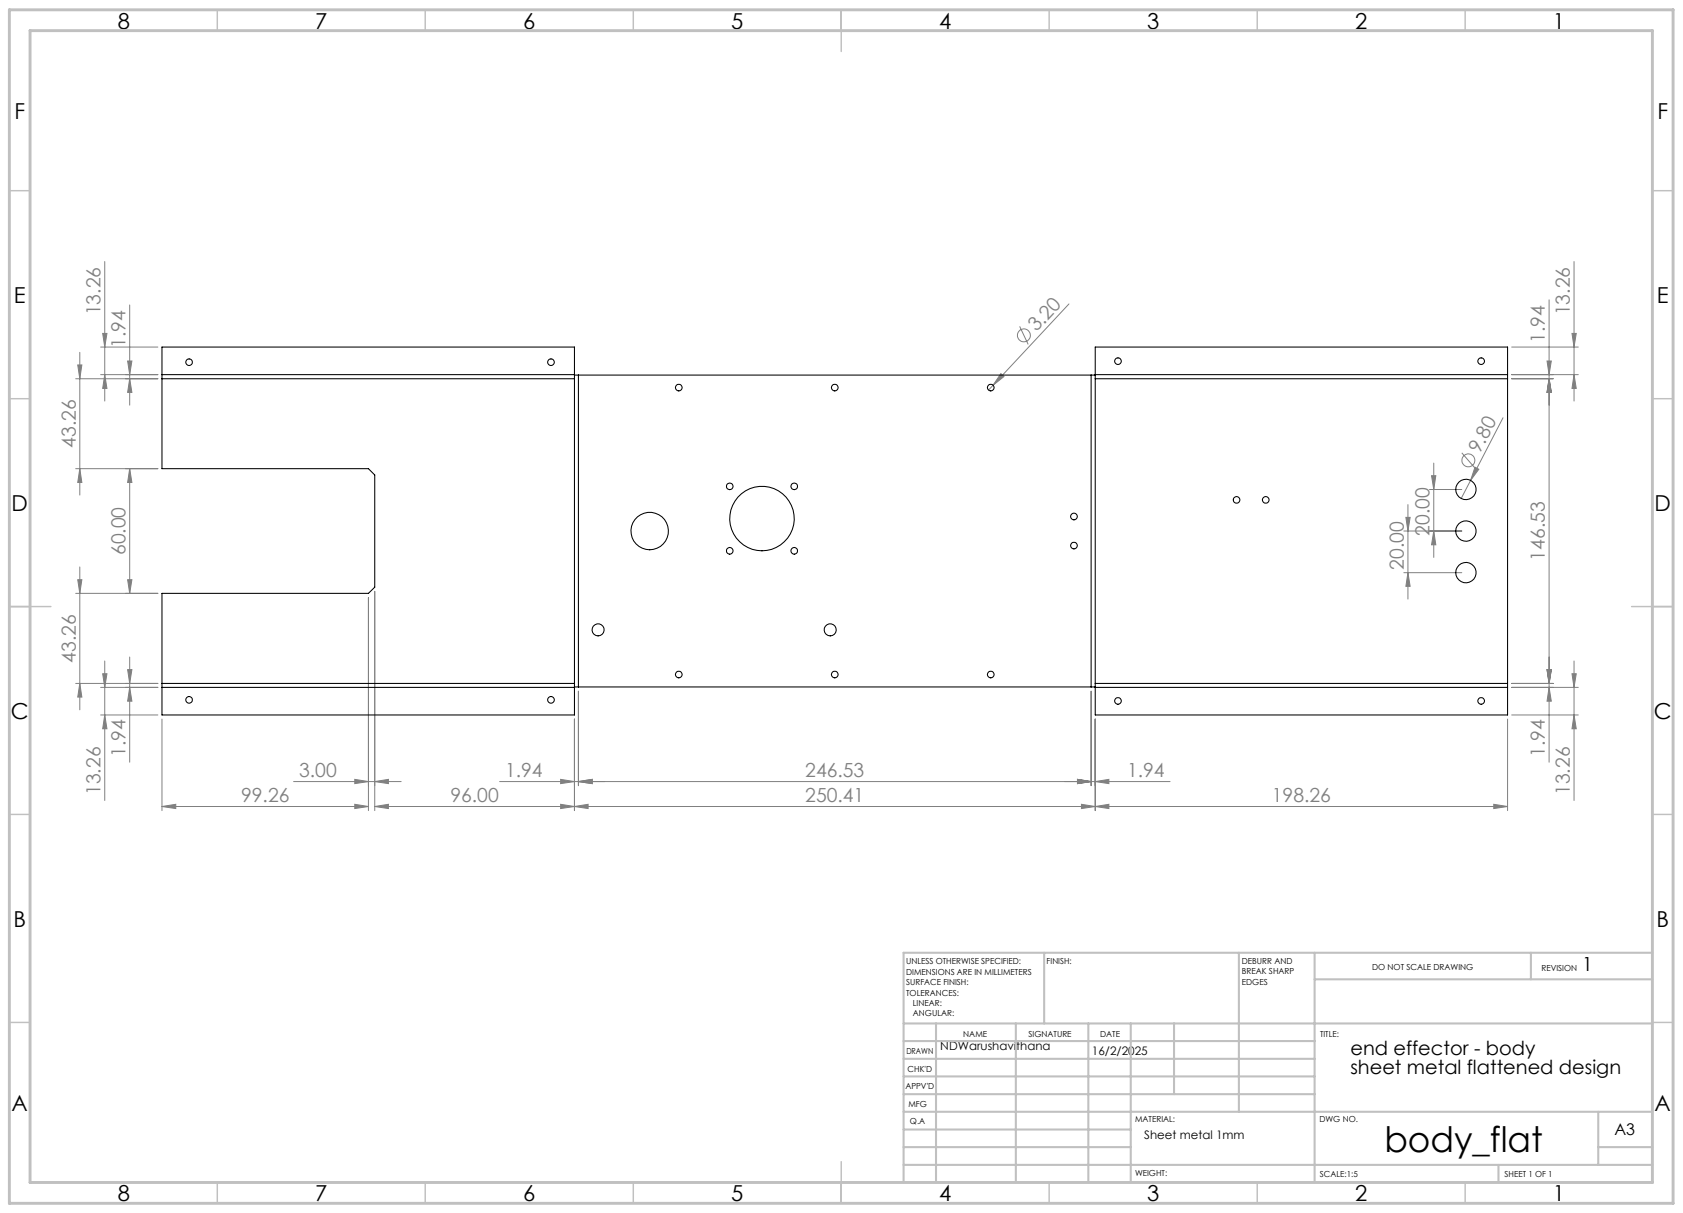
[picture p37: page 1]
FINISH:; DEBURR AND; BREAK SHARP; DO NOT SCALE DRAWING; REVISION; SCALE:1:5; SHEET 1 OF 1

UNLESS OTHERWISE SPECIFIED:
DIMENSIONS ARE IN MILLIMETERS
SURFACE FINISH:
TOLERANCES:
LINEAR:
ANGULAR:

DRAWN | | | 16/2/2025 NDWarushavithana

NAME | SIGNATURE | DATE | | | | TITLE: end effector - body sheet metal flattened design

CHK'D
APPV'D
MFG
Q.A | | | | MATERIAL: Sheet metal 1mm | DWG NO. body_flat | A3

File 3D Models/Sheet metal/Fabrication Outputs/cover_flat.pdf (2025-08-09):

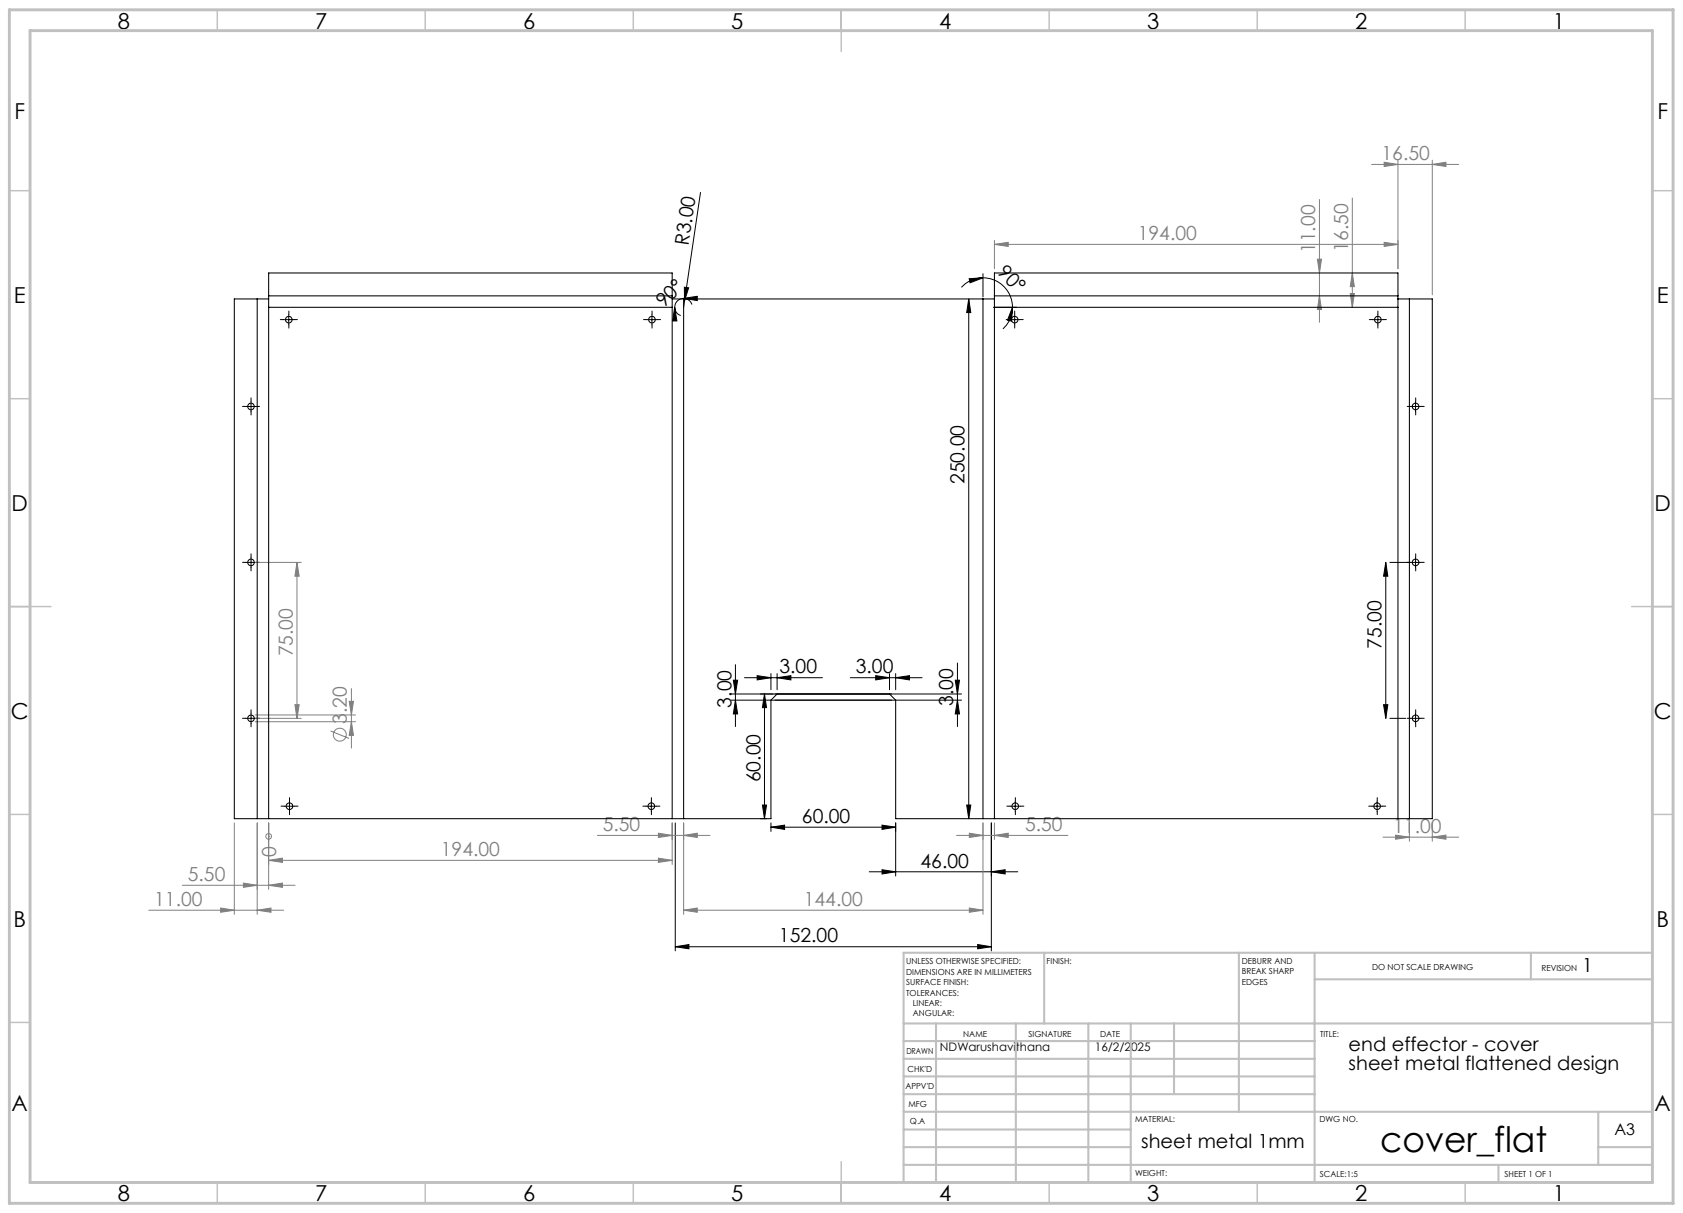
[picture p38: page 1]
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

UNLESS OTHERWISE SPECIFIED:
DIMENSIONS ARE IN MILLIMETERS
SURFACE FINISH:
TOLERANCES:
LINEAR:
ANGULAR:

DRAWN | NDWarushavithana | | 16/2/2025

NAME | SIGNATURE | DATE | | | | TITLE: end effector - cover sheet metal flattened design

CHK'D
APPV'D
MFG
Q.A | | | | MATERIAL: sheet metal 1mm | DWG NO. cover_flat | A3

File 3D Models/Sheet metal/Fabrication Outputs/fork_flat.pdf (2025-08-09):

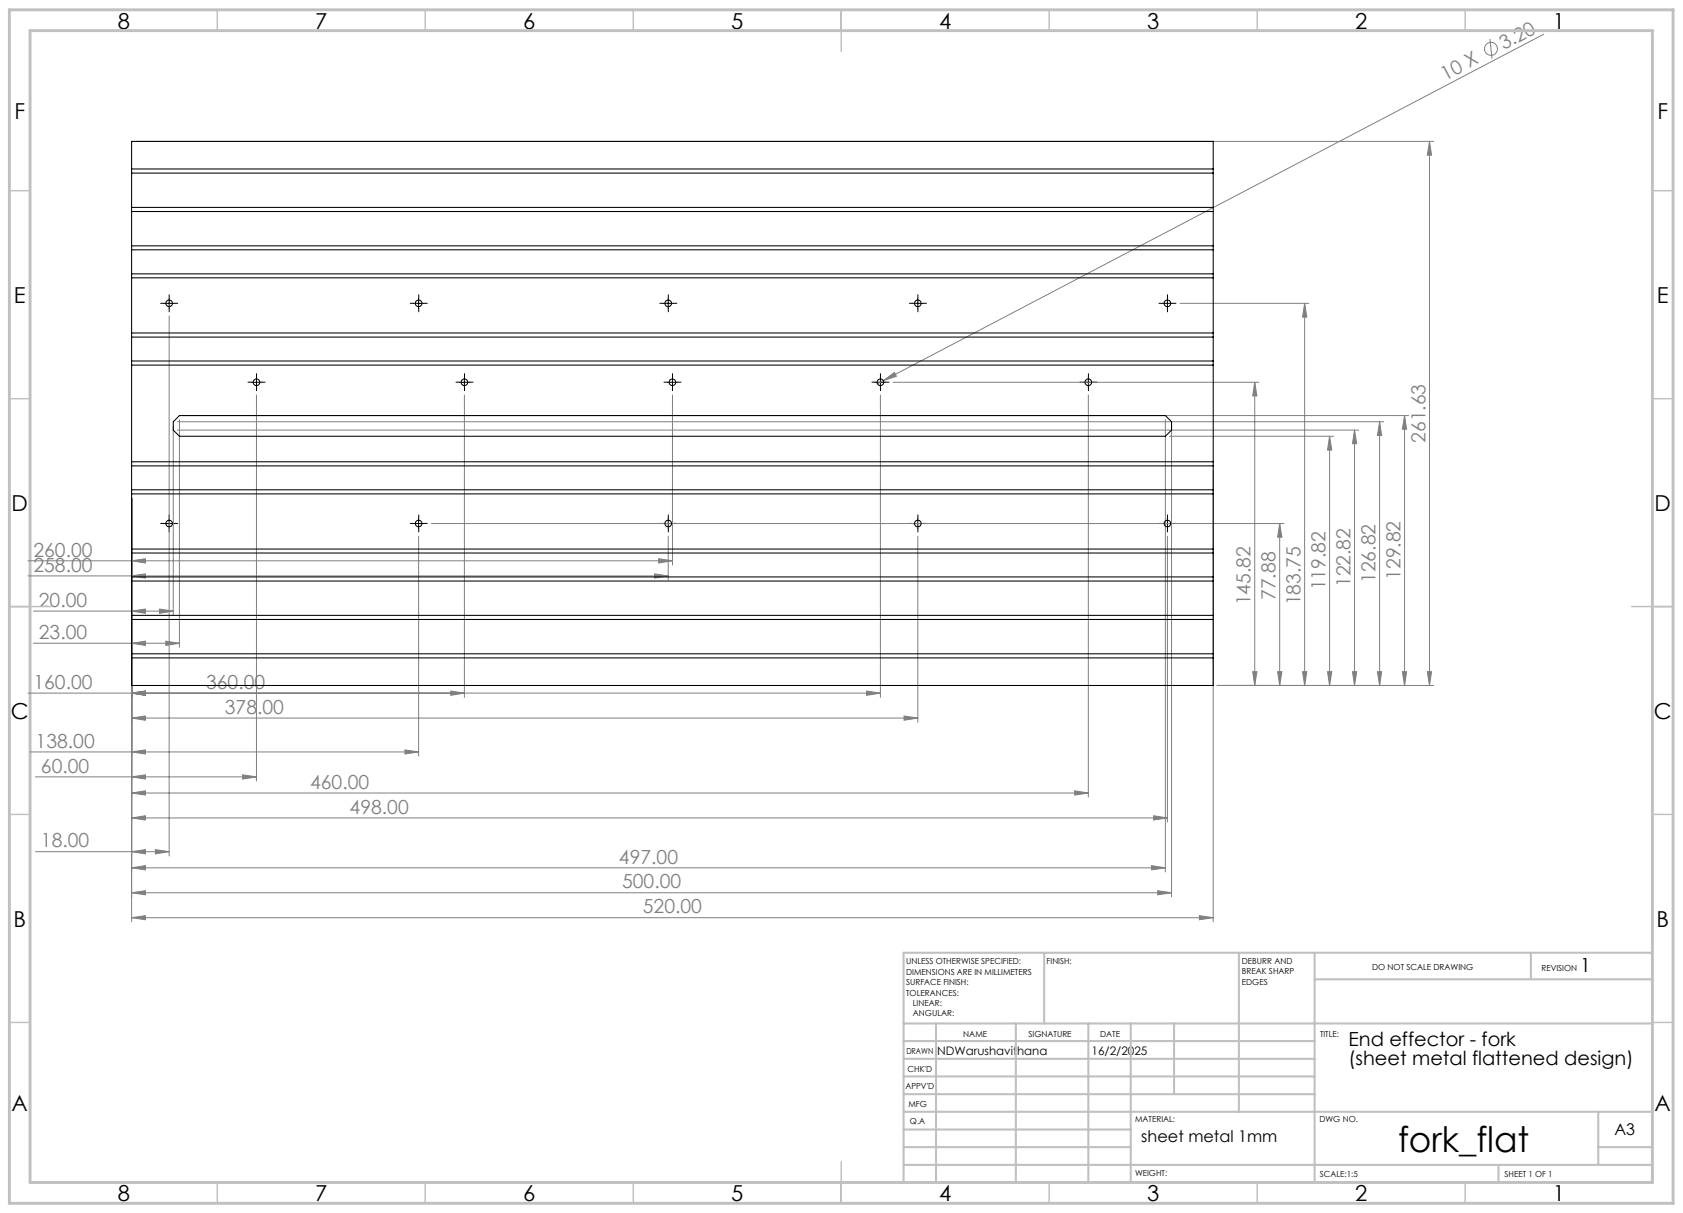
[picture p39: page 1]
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

20.00 | 360.00
23.00
160.00
138.00 | 378.00

UNLESS OTHERWISE SPECIFIED:
DIMENSIONS ARE IN MILLIMETERS
SURFACE FINISH:
TOLERANCES:
LINEAR:
ANGULAR:

NAME | SIGNATURE | DATE | | | | TITLE: End effector - fork (sheet metal flattened design)

DRAWN | NDWarushavithana | | 16/2/2025
CHK'D
APPV'D
MFG
Q.A | | | | MATERIAL: sheet metal 1mm | DWG NO. fork_flat | A3

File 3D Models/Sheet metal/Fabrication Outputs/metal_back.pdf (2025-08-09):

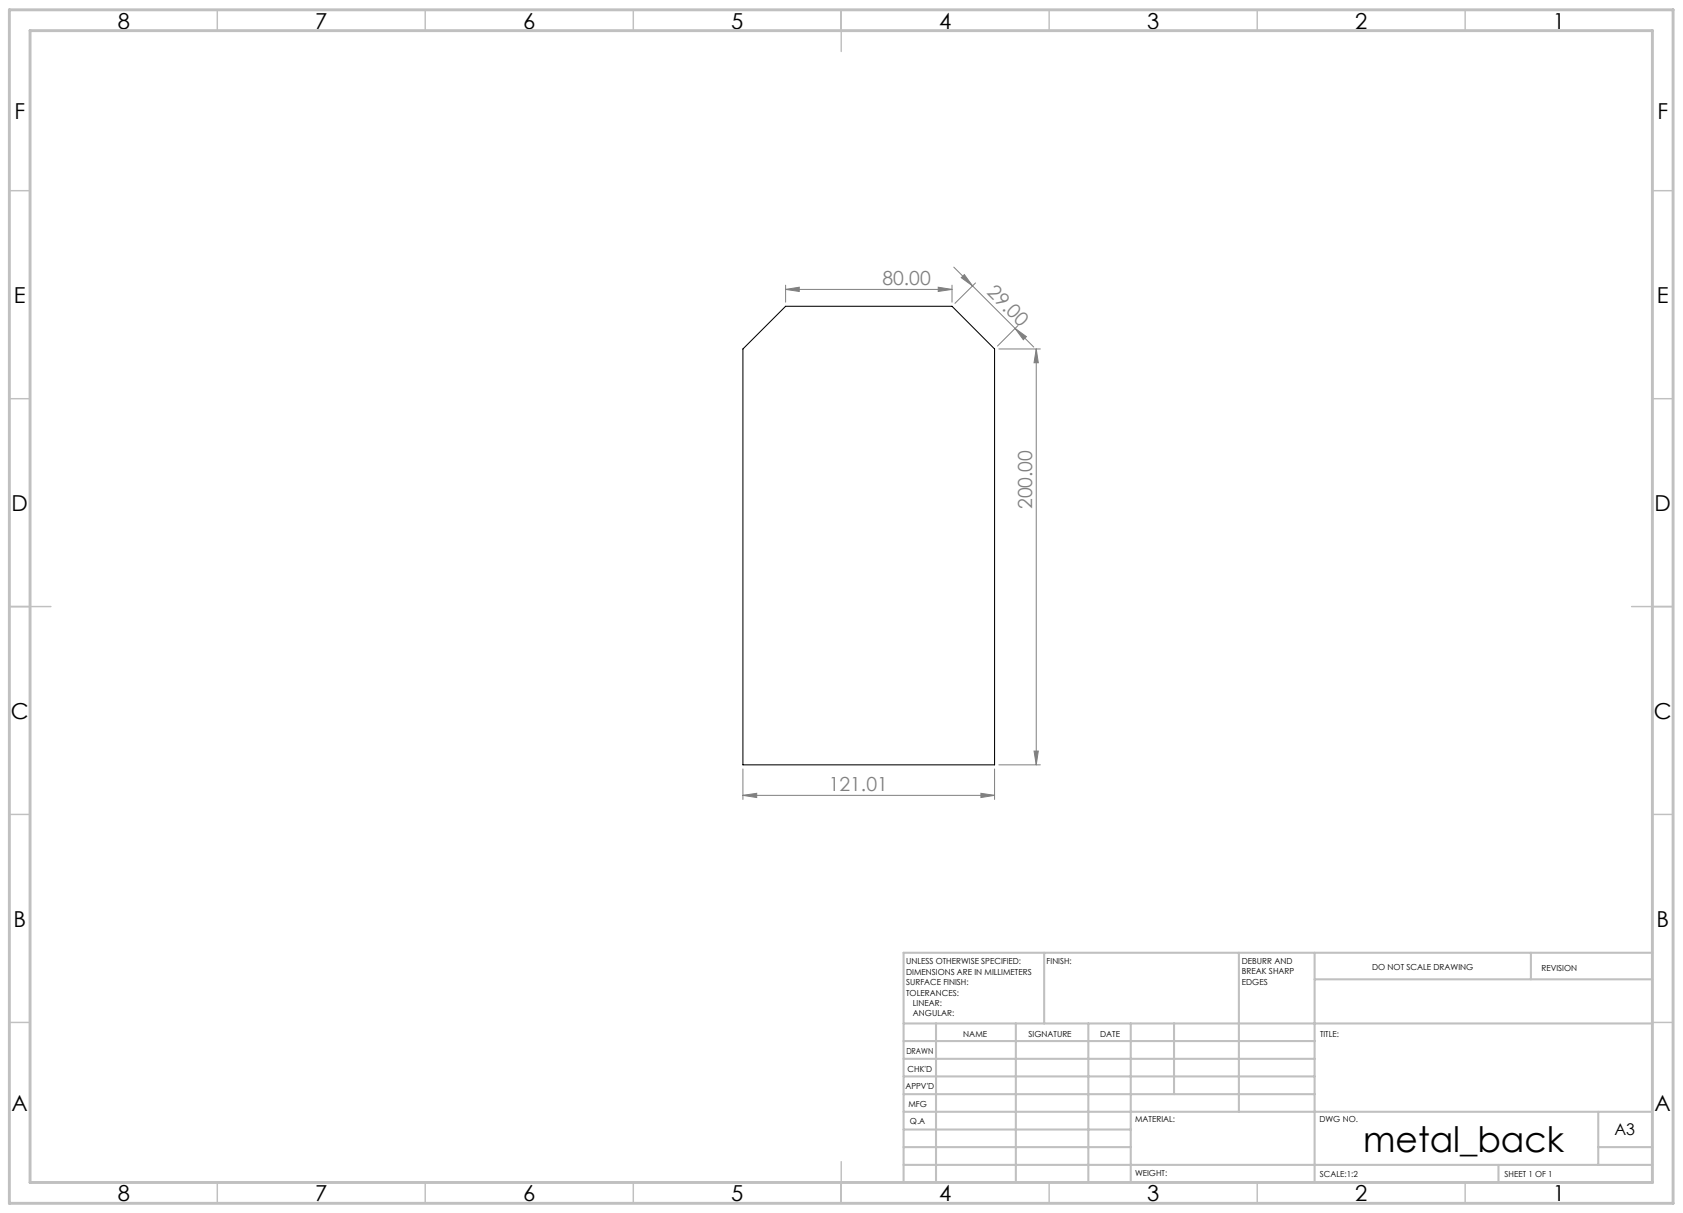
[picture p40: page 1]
FINISH:; DEBURR AND; BREAK SHARP; DO NOT SCALE DRAWING; REVISION; SCALE:1:2; SHEET 1 OF 1

UNLESS OTHERWISE SPECIFIED:
DIMENSIONS ARE IN MILLIMETERS
SURFACE FINISH:
TOLERANCES:
LINEAR:
ANGULAR:

NAME | SIGNATURE | DATE | | | | TITLE:

DRAWN
CHK'D
APPV'D
MFG
Q.A | | | | MATERIAL: | DWG NO. metal_back | A3

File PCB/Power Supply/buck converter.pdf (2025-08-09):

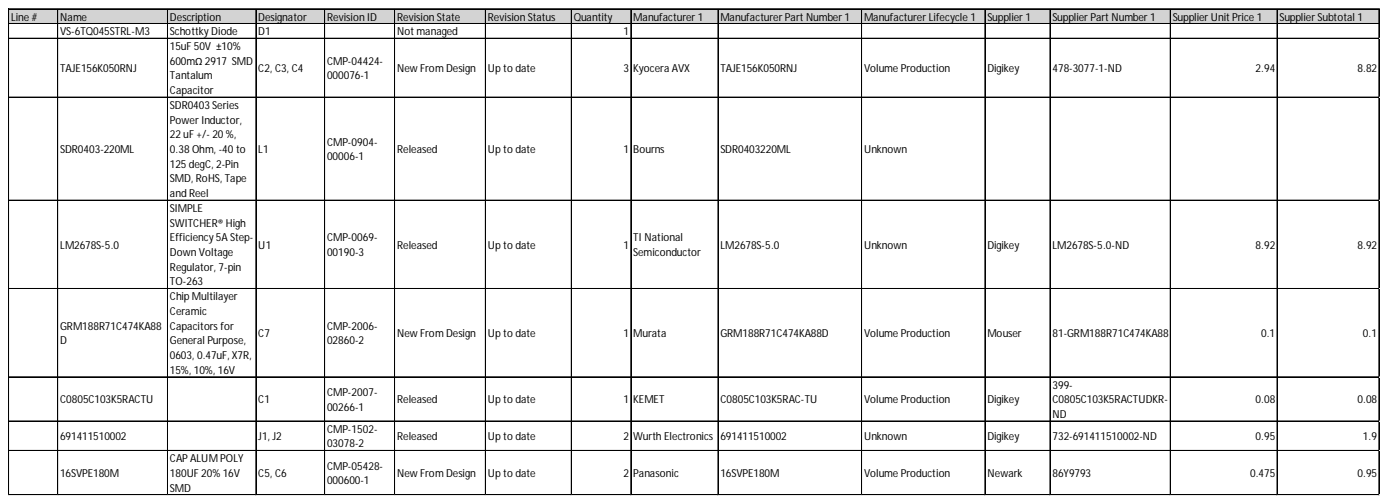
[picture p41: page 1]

Line # | Name | Description | Designator | Revision ID | Revision State | Revision Status | Quantity | Manufacturer 1 | Manufacturer Part Number 1 | Manufacturer Lifecycle 1 | Supplier 1 | Supplier Part Number 1 | Supplier Unit Price 1 | Supplier Subtotal 1

VS-6TQ045STRL-M3 | Schottky Diode | D1 | | Not managed | | 1
TAJE156K050RNJ | 15uF 50V ±10% 600mΩ 2917 SMD Tantalum Capacitor | C2, C3, C4 | CMP-04424-000076-1 | New From Design | Up to date | 3 | Kyocera AVX | TAJE156K050RNJ | Volume Production | Digikey | 478-3077-1-ND | 2.94 | 8.82

SDR0403-220ML | SDR0403 Series Power Inductor, 22 uF +/- 20 %, 0.38 Ohm, -40 to 125 degC, 2-Pin SMD, RoHS, Tape and Reel | L1 | CMP-0904-00006-1 | Released | Up to date | 1 | Bourns | SDR0403220ML | Unknown

LM2678S-5.0 | SIMPLE SWITCHER® High Efficiency 5A Step-Down Voltage Regulator, 7-pin TO-263 | U1 | CMP-0069-00190-3 | Released | Up to date | 1 | TI National Semiconductor | LM2678S-5.0 | Unknown | Digikey | LM2678S-5.0-ND | 8.92 | 8.92

GRM188R71C474KA88 D | Chip Multilayer Ceramic Capacitors for General Purpose, 0603, 0.47uF, X7R, 15%, 10%, 16V | C7 | CMP-2006-02860-2 | New From Design | Up to date | 1 | Murata | GRM188R71C474KA88D | Volume Production | Mouser | 81-GRM188R71C474KA88 | 0.1 | 0.1

C0805C103K5RACTU | | C1 | CMP-2007-00266-1 | Released | Up to date | 1 | KEMET | C0805C103K5RAC-TU | Volume Production | Digikey | 399-C0805C103K5RACTUDKR-ND | 0.08 | 0.08

691411510002 | | J1, J2 | CMP-1502-03078-2 | Released | Up to date | 2 Wurth Electronics | | 691411510002 | Unknown | Digikey | 732-691411510002-ND | 0.95 | 1.9

16SVPE180M | CAP ALUM POLY 180UF 20% 16V SMD | C5, C6 | CMP-05428-000600-1 | New From Design | Up to date | 2 Panasonic | | 16SVPE180M | Volume Production | Newark | 86Y9793 | 0.475 | 0.95

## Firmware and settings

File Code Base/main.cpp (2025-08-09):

#include "main.h"
#include "TofSensor.h"
#include "peripherals.h"
#include "fork.h"
#include "pneumatics.h"
#include "functions.h"
#include "millis.h"

UART uart3(&UBRR0H, &UBRR0L, &UCSR0A, &UCSR0B, &UCSR0C, &UDR0);
UART uart1(&UBRR1H, &UBRR1L, &UCSR1A, &UCSR1B, &UCSR1C, &UDR1);

UART uart0(&UBRR3H, &UBRR3L, &UCSR3A, &UCSR3B, &UCSR3C, &UDR3, PORTE, PORTE5);

int main()
{
  millis_init();
  uart0.init();
  uart3.init();
  setup_seven_segment();

  seven_segment(3);

  uart0.transmit("Booting...\n");
  init_pneumatics();
  tof_init();
  init_fork();
  uart0.transmit("End Effector Ready\n");

  uart3.transmit("UART3 Initialized\n");

  seven_segment(1);

  while (1)
  {
    char command[64] = {0};
    if (uart0.receive_line(command, sizeof(command)))
    {
      process_command(command);
    }
  }

  while (1)
  {
    // activate_solenoid(0);
    // activate_solenoid(1);
    // activate_solenoid(2);
    // activate_solenoid(3);
    // activate_solenoid(4);
    // _delay_ms(300);

    // deactivate_solenoid(0);
    // deactivate_solenoid(1);
    // deactivate_solenoid(2);
    // deactivate_solenoid(3);
    // deactivate_solenoid(4);
    // _delay_ms(300);
  }

  while (1)
  {
  }
}

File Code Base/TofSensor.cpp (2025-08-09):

#include <math.h>
#include "TofSensor.h"
#include "uart.h"

extern UART uart0;
extern UART uart1;

uint8_t queryCommand[8] = {0x57, 0x10, 0xFF, 0xFF, 0x03, 0xFF, 0xFF, 0x66};
uint8_t frame[FRAME_SIZE];
float distances[4];


constexpr float DEG2RAD = 3.14159265 / 180.0;

// You can adjust FoV if your sensor uses a different value
constexpr float H_FOV_DEG = 45.0;
constexpr float V_FOV_DEG = 45.0;


void tof_init()
{
    uart1.init(); // Initialize UART1
}

void read_tof()
{
    uart0.transmit("\n\n");

    sendQuery(); // Send the query command to the sensor
    
    // Wait for header
    while (true)
    {
        if (uart1.read() == HEADER_BYTE_0)
        {
            uart1.read(); // consume second header byte
            break;
        }
    }
    

    // Read the rest of the frame (FRAME_SIZE - 2 already read)
    int bytesRead = 0;
    while (bytesRead < FRAME_SIZE - 2)
    {
        if(uart1.available())
        {
            frame[bytesRead++] = uart1.read();
        }
    }
    //uart0.transmit("Frame received\n");

    // Parse and print corner distances (indexes: 0, 7, 56, 63)
    int dataStart = 7; // Skip ID (1), timestamp (3), and some flags (3)
    int distances_index = 0;
    for (int i = 0; i < DATA_POINTS; i++)
    {
        int offset = dataStart + i * POINT_SIZE;
        if (offset + 2 >= FRAME_SIZE)
            break;

        float distance = calculateValue(frame[offset], frame[offset + 1], frame[offset + 2]);

        // Only print four corners
        //if (i == 35 || i == 36 || i == 43 || i == 44)
        if (i == 0 || i == 7 || i == 56 || i == 63)
        {
            printDistance(i, distance);
            distances[distances_index] = distance;
            distances_index++;
        }
    }

    calculateAngleFromCorners(distances[0], distances[1], distances[2], distances[3]);

    //_delay_ms(2000); // Query interval
}






// Estimate the angle (in degrees) of the object relative to the center
// from 4 corner distances (in mm or cm — consistent units)
float calculateAngleFromCorners(float d0, float d7, float d56, float d63)
{
    // Pixel grid positions for the 4 corners
    int x0 = 0, y0 = 0;
    int x7 = 7, y7 = 0;
    int x56 = 0, y56 = 7;
    int x63 = 7, y63 = 7;

    // Angle per pixel
    float hAnglePerPixel = H_FOV_DEG / 7.0;
    float vAnglePerPixel = V_FOV_DEG / 7.0;

    // Convert pixel positions to angles (centered at 0)
    float ax0 = (x0 - 3.5) * hAnglePerPixel;
    float ay0 = (y0 - 3.5) * vAnglePerPixel;
    float ax7 = (x7 - 3.5) * hAnglePerPixel;
    float ay7 = (y7 - 3.5) * vAnglePerPixel;
    float ax56 = (x56 - 3.5) * hAnglePerPixel;
    float ay56 = (y56 - 3.5) * vAnglePerPixel;
    float ax63 = (x63 - 3.5) * hAnglePerPixel;
    float ay63 = (y63 - 3.5) * vAnglePerPixel;

    // Convert to 3D coordinates
    float x_sum = d0 * tan(ax0 * DEG2RAD) +
                  d7 * tan(ax7 * DEG2RAD) +
                  d56 * tan(ax56 * DEG2RAD) +
                  d63 * tan(ax63 * DEG2RAD);

    float y_sum = d0 * tan(ay0 * DEG2RAD) +
                  d7 * tan(ay7 * DEG2RAD) +
                  d56 * tan(ay56 * DEG2RAD) +
                  d63 * tan(ay63 * DEG2RAD);

    float z_sum = d0 + d7 + d56 + d63;

    // Average to get direction vector
    float x_avg = x_sum / 4.0;
    float y_avg = y_sum / 4.0;
    float z_avg = z_sum / 4.0;

    // Compute angle from center in degrees
    float horizontalAngle = 10*atan2(x_avg, z_avg) * 180.0 / 3.14159265;
    float verticalAngle = 10*atan2(y_avg, z_avg) * 180.0 / 3.14159265;

    uart0.transmit("Horizontal Angle: ");
    uart0.transmit(horizontalAngle, 2);
    uart0.transmit(" Vertical Angle: ");
    uart0.transmit(verticalAngle, 2);
    uart0.transmit("\n");

    // Optional: return horizontal only, or both as struct if needed
    return horizontalAngle; // or verticalAngle
}

// Parse int24 as per protocol: (b0 << 8 | b1 << 16 | b2 << 24) / 256
int32_t parse_int24(uint8_t b0, uint8_t b1, uint8_t b2)
{
    int32_t value = ((int32_t)b2 << 16) | ((int32_t)b1 << 8) | b0;
    // Sign extend if the top bit is set (for 24-bit signed)
    if (value & 0x800000)
        value |= 0xFF000000;
    return value;
}

float calculateValue(uint8_t b0, uint8_t b1, uint8_t b2)
{
    int32_t temp = parse_int24(b0, b1, b2);
    return temp / 1000.0; //mm 
}

void printDistance(int index, float raw)
{
    float mm = raw;
    uart0.transmit("Index ");
    uart0.transmit(" ");
    //uart0.transmit((float)index, 0);
    uart0.transmit(": ");
    uart0.transmit(mm, 3);
    uart0.transmit(" mm\n");
}

void sendQuery()
{
    uart1.transmit(queryCommand, 8);
}
